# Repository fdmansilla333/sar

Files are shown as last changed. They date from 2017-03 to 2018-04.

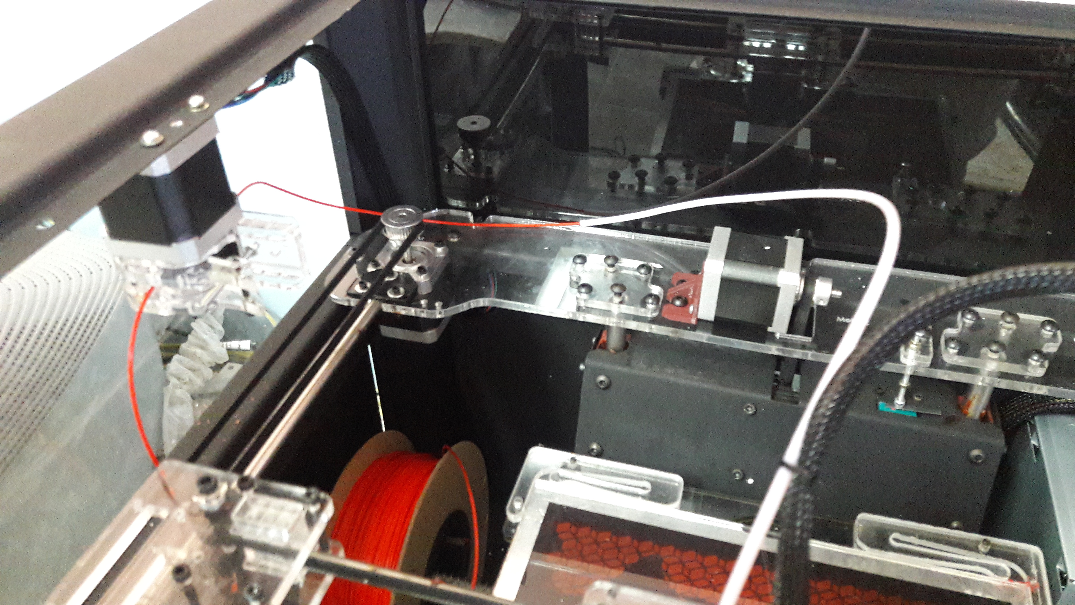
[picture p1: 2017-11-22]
Material/20170808_095417.jpg

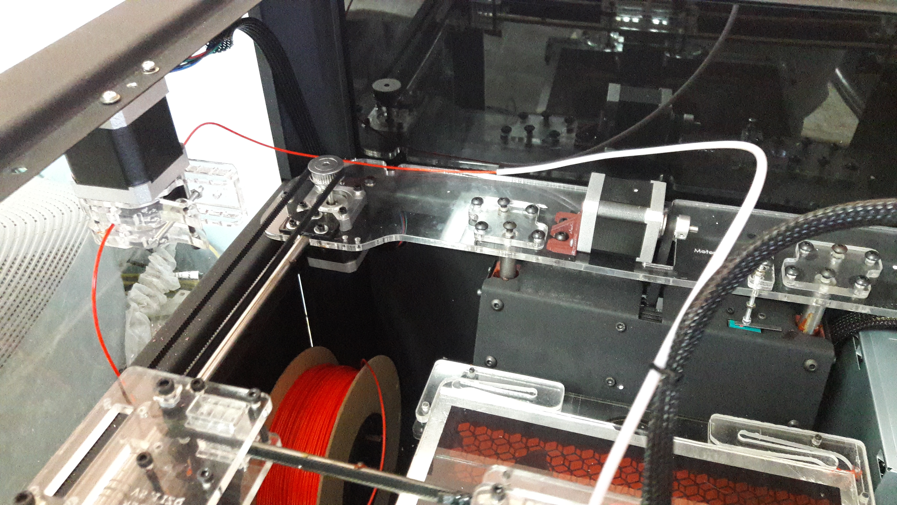
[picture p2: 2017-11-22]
Material/20170808_095419.jpg

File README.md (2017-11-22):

# sar
Sistema Autónomo Robótico

Autores:
->Mansilla Damián
->Schlapp Agustin

*Directorios
#App
Posee la aplicación y las pruebas sobre Nodejs, Johnny-five, Angular4.5, Mongo, Express. (Stack MEAN)

#Capitulos
Posee los capítulos del informe de la Tesis

#Documentacion
Contiene la documentación de los códigos fuentes de Arduino.

#Material
Contiene material bibliografíco

#Modelos3d
Posee los modelos realizados con Sketchup (diseños --> STL) y Cura (STL -> Gcode) para imprimir en 3d.

#Plantilla de casos de prueba de sensores y actuadores
Contiene todos los casos de prueba realizados sobre los sensores y actuadores. Las pruebas testean el funcionamiento básico.

#Test de sensores y actuadores Arduino
Contiene todos los códigos de prueba sobre cada actuador y sensor compatible con Arduino.

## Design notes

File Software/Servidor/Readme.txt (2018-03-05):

Comando para importar datos a mongo un arreglo json
mongoimport -c temperaturas -d sar --mode upsert --file temperaturas.json --jsonArray
Para iniciar ejecutar iniciar.bat(Windows) iniciar.sh(linux)

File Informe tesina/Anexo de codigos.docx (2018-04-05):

# Anexo de códigos

En este anexo se adjuntaron los códigos más relevantes, tanto del lado del cliente como del servidor, que se desarrollaron para el funcionamiento del SAR.

## Códigos del lado del servidor

### Código StandarFirmata utilizado en el Arduino MEGA

/*

Firmata is a generic protocol for communicating with microcontrollers

from software on a host computer. It is intended to work with

any host computer software package.

To download a host software package, please click on the following link

to open the list of Firmata client libraries in your default browser.

https://github.com/firmata/arduino#firmata-client-libraries

Copyright (C) 2006-2008 Hans-Christoph Steiner. All rights reserved.

Copyright (C) 2010-2011 Paul Stoffregen. All rights reserved.

Copyright (C) 2009 Shigeru Kobayashi. All rights reserved.

Copyright (C) 2009-2016 Jeff Hoefs. All rights reserved.

This library is free software; you can redistribute it and/or

modify it under the terms of the GNU Lesser General Public

License as published by the Free Software Foundation; either

version 2.1 of the License, or (at your option) any later version.

See file LICENSE.txt for further informations on licensing terms.

Last updated October 16th, 2016

*/

#include <Servo.h>

#include <Wire.h>

#include <Firmata.h>

#define I2C_WRITE B00000000

#define I2C_READ B00001000

#define I2C_READ_CONTINUOUSLY B00010000

#define I2C_STOP_READING B00011000

#define I2C_READ_WRITE_MODE_MASK B00011000

#define I2C_10BIT_ADDRESS_MODE_MASK B00100000

#define I2C_END_TX_MASK B01000000

#define I2C_STOP_TX 1

#define I2C_RESTART_TX 0

#define I2C_MAX_QUERIES 8

#define I2C_REGISTER_NOT_SPECIFIED -1

// the minimum interval for sampling analog input

#define MINIMUM_SAMPLING_INTERVAL 1

/*==============================================================================

* GLOBAL VARIABLES

*============================================================================*/

#ifdef FIRMATA_SERIAL_FEATURE

SerialFirmata serialFeature;

#endif

/* analog inputs */

int analogInputsToReport = 0; // bitwise array to store pin reporting

/* digital input ports */

byte reportPINs[TOTAL_PORTS]; // 1 = report this port, 0 = silence

byte previousPINs[TOTAL_PORTS]; // previous 8 bits sent

/* pins configuration */

byte portConfigInputs[TOTAL_PORTS]; // each bit: 1 = pin in INPUT, 0 = anything else

/* timer variables */

unsigned long currentMillis; // store the current value from millis()

unsigned long previousMillis; // for comparison with currentMillis

unsigned int samplingInterval = 19; // how often to run the main loop (in ms)

/* i2c data */

struct i2c_device_info {

byte addr;

int reg;

byte bytes;

byte stopTX;

};

/* for i2c read continuous more */

i2c_device_info query[I2C_MAX_QUERIES];

byte i2cRxData[64];

boolean isI2CEnabled = false;

signed char queryIndex = -1;

// default delay time between i2c read request and Wire.requestFrom()

unsigned int i2cReadDelayTime = 0;

Servo servos[MAX_SERVOS];

byte servoPinMap[TOTAL_PINS];

byte detachedServos[MAX_SERVOS];

byte detachedServoCount = 0;

byte servoCount = 0;

boolean isResetting = false;

// Forward declare a few functions to avoid compiler errors with older versions

// of the Arduino IDE.

void setPinModeCallback(byte, int);

void reportAnalogCallback(byte analogPin, int value);

void sysexCallback(byte, byte, byte*);

/* utility functions */

void wireWrite(byte data)

{

#if ARDUINO >= 100

Wire.write((byte)data);

#else

Wire.send(data);

#endif

}

byte wireRead(void)

{

#if ARDUINO >= 100

return Wire.read();

#else

return Wire.receive();

#endif

}

/*==============================================================================

* FUNCTIONS

*============================================================================*/

void attachServo(byte pin, int minPulse, int maxPulse)

{

if (servoCount < MAX_SERVOS) {

// reuse indexes of detached servos until all have been reallocated

if (detachedServoCount > 0) {

servoPinMap[pin] = detachedServos[detachedServoCount - 1];

if (detachedServoCount > 0) detachedServoCount--;

} else {

servoPinMap[pin] = servoCount;

servoCount++;

}

if (minPulse > 0 && maxPulse > 0) {

servos[servoPinMap[pin]].attach(PIN_TO_DIGITAL(pin), minPulse, maxPulse);

} else {

servos[servoPinMap[pin]].attach(PIN_TO_DIGITAL(pin));

}

} else {

Firmata.sendString("Max servos attached");

}

}

void detachServo(byte pin)

{

servos[servoPinMap[pin]].detach();

// if we're detaching the last servo, decrement the count

// otherwise store the index of the detached servo

if (servoPinMap[pin] == servoCount && servoCount > 0) {

servoCount--;

} else if (servoCount > 0) {

// keep track of detached servos because we want to reuse their indexes

// before incrementing the count of attached servos

detachedServoCount++;

detachedServos[detachedServoCount - 1] = servoPinMap[pin];

}

servoPinMap[pin] = 255;

}

void enableI2CPins()

{

byte i;

// is there a faster way to do this? would probaby require importing

// Arduino.h to get SCL and SDA pins

for (i = 0; i < TOTAL_PINS; i++) {

if (IS_PIN_I2C(i)) {

// mark pins as i2c so they are ignore in non i2c data requests

setPinModeCallback(i, PIN_MODE_I2C);

}

}

isI2CEnabled = true;

Wire.begin();

}

/* disable the i2c pins so they can be used for other functions */

void disableI2CPins() {

isI2CEnabled = false;

// disable read continuous mode for all devices

queryIndex = -1;

}

void readAndReportData(byte address, int theRegister, byte numBytes, byte stopTX) {

// allow I2C requests that don't require a register read

// for example, some devices using an interrupt pin to signify new data available

// do not always require the register read so upon interrupt you call Wire.requestFrom()

if (theRegister != I2C_REGISTER_NOT_SPECIFIED) {

Wire.beginTransmission(address);

wireWrite((byte)theRegister);

Wire.endTransmission(stopTX); // default = true

// do not set a value of 0

if (i2cReadDelayTime > 0) {

// delay is necessary for some devices such as WiiNunchuck

delayMicroseconds(i2cReadDelayTime);

}

} else {

theRegister = 0; // fill the register with a dummy value

}

Wire.requestFrom(address, numBytes); // all bytes are returned in requestFrom

// check to be sure correct number of bytes were returned by slave

if (numBytes < Wire.available()) {

Firmata.sendString("I2C: Too many bytes received");

} else if (numBytes > Wire.available()) {

Firmata.sendString("I2C: Too few bytes received");

}

i2cRxData[0] = address;

i2cRxData[1] = theRegister;

for (int i = 0; i < numBytes && Wire.available(); i++) {

i2cRxData[2 + i] = wireRead();

}

// send slave address, register and received bytes

Firmata.sendSysex(SYSEX_I2C_REPLY, numBytes + 2, i2cRxData);

}

void outputPort(byte portNumber, byte portValue, byte forceSend)

{

// pins not configured as INPUT are cleared to zeros

portValue = portValue & portConfigInputs[portNumber];

// only send if the value is different than previously sent

if (forceSend || previousPINs[portNumber] != portValue) {

Firmata.sendDigitalPort(portNumber, portValue);

previousPINs[portNumber] = portValue;

}

}

/* -----------------------------------------------------------------------------

* check all the active digital inputs for change of state, then add any events

* to the Serial output queue using Serial.print() */

void checkDigitalInputs(void)

{

/* Using non-looping code allows constants to be given to readPort().

* The compiler will apply substantial optimizations if the inputs

* to readPort() are compile-time constants. */

if (TOTAL_PORTS > 0 && reportPINs[0]) outputPort(0, readPort(0, portConfigInputs[0]), false);

if (TOTAL_PORTS > 1 && reportPINs[1]) outputPort(1, readPort(1, portConfigInputs[1]), false);

if (TOTAL_PORTS > 2 && reportPINs[2]) outputPort(2, readPort(2, portConfigInputs[2]), false);

if (TOTAL_PORTS > 3 && reportPINs[3]) outputPort(3, readPort(3, portConfigInputs[3]), false);

if (TOTAL_PORTS > 4 && reportPINs[4]) outputPort(4, readPort(4, portConfigInputs[4]), false);

if (TOTAL_PORTS > 5 && reportPINs[5]) outputPort(5, readPort(5, portConfigInputs[5]), false);

if (TOTAL_PORTS > 6 && reportPINs[6]) outputPort(6, readPort(6, portConfigInputs[6]), false);

if (TOTAL_PORTS > 7 && reportPINs[7]) outputPort(7, readPort(7, portConfigInputs[7]), false);

if (TOTAL_PORTS > 8 && reportPINs[8]) outputPort(8, readPort(8, portConfigInputs[8]), false);

if (TOTAL_PORTS > 9 && reportPINs[9]) outputPort(9, readPort(9, portConfigInputs[9]), false);

if (TOTAL_PORTS > 10 && reportPINs[10]) outputPort(10, readPort(10, portConfigInputs[10]), false);

if (TOTAL_PORTS > 11 && reportPINs[11]) outputPort(11, readPort(11, portConfigInputs[11]), false);

if (TOTAL_PORTS > 12 && reportPINs[12]) outputPort(12, readPort(12, portConfigInputs[12]), false);

if (TOTAL_PORTS > 13 && reportPINs[13]) outputPort(13, readPort(13, portConfigInputs[13]), false);

if (TOTAL_PORTS > 14 && reportPINs[14]) outputPort(14, readPort(14, portConfigInputs[14]), false);

if (TOTAL_PORTS > 15 && reportPINs[15]) outputPort(15, readPort(15, portConfigInputs[15]), false);

}

// -----------------------------------------------------------------------------

/* sets the pin mode to the correct state and sets the relevant bits in the

* two bit-arrays that track Digital I/O and PWM status

*/

void setPinModeCallback(byte pin, int mode)

{

if (Firmata.getPinMode(pin) == PIN_MODE_IGNORE)

return;

if (Firmata.getPinMode(pin) == PIN_MODE_I2C && isI2CEnabled && mode != PIN_MODE_I2C) {

// disable i2c so pins can be used for other functions

// the following if statements should reconfigure the pins properly

disableI2CPins();

}

if (IS_PIN_DIGITAL(pin) && mode != PIN_MODE_SERVO) {

if (servoPinMap[pin] < MAX_SERVOS && servos[servoPinMap[pin]].attached()) {

detachServo(pin);

}

}

if (IS_PIN_ANALOG(pin)) {

reportAnalogCallback(PIN_TO_ANALOG(pin), mode == PIN_MODE_ANALOG ? 1 : 0); // turn on/off reporting

}

if (IS_PIN_DIGITAL(pin)) {

if (mode == INPUT || mode == PIN_MODE_PULLUP) {

portConfigInputs[pin / 8] |= (1 << (pin & 7));

} else {

portConfigInputs[pin / 8] &= ~(1 << (pin & 7));

}

}

Firmata.setPinState(pin, 0);

switch (mode) {

case PIN_MODE_ANALOG:

if (IS_PIN_ANALOG(pin)) {

if (IS_PIN_DIGITAL(pin)) {

pinMode(PIN_TO_DIGITAL(pin), INPUT); // disable output driver

#if ARDUINO <= 100

// deprecated since Arduino 1.0.1 - TODO: drop support in Firmata 2.6

digitalWrite(PIN_TO_DIGITAL(pin), LOW); // disable internal pull-ups

#endif

}

Firmata.setPinMode(pin, PIN_MODE_ANALOG);

}

break;

case INPUT:

if (IS_PIN_DIGITAL(pin)) {

pinMode(PIN_TO_DIGITAL(pin), INPUT); // disable output driver

#if ARDUINO <= 100

// deprecated since Arduino 1.0.1 - TODO: drop support in Firmata 2.6

digitalWrite(PIN_TO_DIGITAL(pin), LOW); // disable internal pull-ups

#endif

Firmata.setPinMode(pin, INPUT);

}

break;

case PIN_MODE_PULLUP:

if (IS_PIN_DIGITAL(pin)) {

pinMode(PIN_TO_DIGITAL(pin), INPUT_PULLUP);

Firmata.setPinMode(pin, PIN_MODE_PULLUP);

Firmata.setPinState(pin, 1);

}

break;

case OUTPUT:

if (IS_PIN_DIGITAL(pin)) {

if (Firmata.getPinMode(pin) == PIN_MODE_PWM) {

// Disable PWM if pin mode was previously set to PWM.

digitalWrite(PIN_TO_DIGITAL(pin), LOW);

}

pinMode(PIN_TO_DIGITAL(pin), OUTPUT);

Firmata.setPinMode(pin, OUTPUT);

}

break;

case PIN_MODE_PWM:

if (IS_PIN_PWM(pin)) {

pinMode(PIN_TO_PWM(pin), OUTPUT);

analogWrite(PIN_TO_PWM(pin), 0);

Firmata.setPinMode(pin, PIN_MODE_PWM);

}

break;

case PIN_MODE_SERVO:

if (IS_PIN_DIGITAL(pin)) {

Firmata.setPinMode(pin, PIN_MODE_SERVO);

if (servoPinMap[pin] == 255 || !servos[servoPinMap[pin]].attached()) {

// pass -1 for min and max pulse values to use default values set

// by Servo library

attachServo(pin, -1, -1);

}

}

break;

case PIN_MODE_I2C:

if (IS_PIN_I2C(pin)) {

// mark the pin as i2c

// the user must call I2C_CONFIG to enable I2C for a device

Firmata.setPinMode(pin, PIN_MODE_I2C);

}

break;

case PIN_MODE_SERIAL:

#ifdef FIRMATA_SERIAL_FEATURE

serialFeature.handlePinMode(pin, PIN_MODE_SERIAL);

#endif

break;

default:

Firmata.sendString("Unknown pin mode"); // TODO: put error msgs in EEPROM

}

// TODO: save status to EEPROM here, if changed

}

/*

* Sets the value of an individual pin. Useful if you want to set a pin value but

* are not tracking the digital port state.

* Can only be used on pins configured as OUTPUT.

* Cannot be used to enable pull-ups on Digital INPUT pins.

*/

void setPinValueCallback(byte pin, int value)

{

if (pin < TOTAL_PINS && IS_PIN_DIGITAL(pin)) {

if (Firmata.getPinMode(pin) == OUTPUT) {

Firmata.setPinState(pin, value);

digitalWrite(PIN_TO_DIGITAL(pin), value);

}

}

}

void analogWriteCallback(byte pin, int value)

{

if (pin < TOTAL_PINS) {

switch (Firmata.getPinMode(pin)) {

case PIN_MODE_SERVO:

if (IS_PIN_DIGITAL(pin))

servos[servoPinMap[pin]].write(value);

Firmata.setPinState(pin, value);

break;

case PIN_MODE_PWM:

if (IS_PIN_PWM(pin))

analogWrite(PIN_TO_PWM(pin), value);

Firmata.setPinState(pin, value);

break;

}

}

}

void digitalWriteCallback(byte port, int value)

{

byte pin, lastPin, pinValue, mask = 1, pinWriteMask = 0;

if (port < TOTAL_PORTS) {

// create a mask of the pins on this port that are writable.

lastPin = port * 8 + 8;

if (lastPin > TOTAL_PINS) lastPin = TOTAL_PINS;

for (pin = port * 8; pin < lastPin; pin++) {

// do not disturb non-digital pins (eg, Rx & Tx)

if (IS_PIN_DIGITAL(pin)) {

// do not touch pins in PWM, ANALOG, SERVO or other modes

if (Firmata.getPinMode(pin) == OUTPUT || Firmata.getPinMode(pin) == INPUT) {

pinValue = ((byte)value & mask) ? 1 : 0;

if (Firmata.getPinMode(pin) == OUTPUT) {

pinWriteMask |= mask;

} else if (Firmata.getPinMode(pin) == INPUT && pinValue == 1 && Firmata.getPinState(pin) != 1) {

// only handle INPUT here for backwards compatibility

#if ARDUINO > 100

pinMode(pin, INPUT_PULLUP);

#else

// only write to the INPUT pin to enable pullups if Arduino v1.0.0 or earlier

pinWriteMask |= mask;

#endif

}

Firmata.setPinState(pin, pinValue);

}

}

mask = mask << 1;

}

writePort(port, (byte)value, pinWriteMask);

}

}

// -----------------------------------------------------------------------------

/* sets bits in a bit array (int) to toggle the reporting of the analogIns

*/

//void FirmataClass::setAnalogPinReporting(byte pin, byte state) {

//}

void reportAnalogCallback(byte analogPin, int value)

{

if (analogPin < TOTAL_ANALOG_PINS) {

if (value == 0) {

analogInputsToReport = analogInputsToReport & ~ (1 << analogPin);

} else {

analogInputsToReport = analogInputsToReport | (1 << analogPin);

// prevent during system reset or all analog pin values will be reported

// which may report noise for unconnected analog pins

if (!isResetting) {

// Send pin value immediately. This is helpful when connected via

// ethernet, wi-fi or bluetooth so pin states can be known upon

// reconnecting.

Firmata.sendAnalog(analogPin, analogRead(analogPin));

}

}

}

// TODO: save status to EEPROM here, if changed

}

void reportDigitalCallback(byte port, int value)

{

if (port < TOTAL_PORTS) {

reportPINs[port] = (byte)value;

// Send port value immediately. This is helpful when connected via

// ethernet, wi-fi or bluetooth so pin states can be known upon

// reconnecting.

if (value) outputPort(port, readPort(port, portConfigInputs[port]), true);

}

// do not disable analog reporting on these 8 pins, to allow some

// pins used for digital, others analog. Instead, allow both types

// of reporting to be enabled, but check if the pin is configured

// as analog when sampling the analog inputs. Likewise, while

// scanning digital pins, portConfigInputs will mask off values from any

// pins configured as analog

}

/*==============================================================================

* SYSEX-BASED commands

*============================================================================*/

void sysexCallback(byte command, byte argc, byte *argv)

{

byte mode;

byte stopTX;

byte slaveAddress;

byte data;

int slaveRegister;

unsigned int delayTime;

switch (command) {

case I2C_REQUEST:

mode = argv[1] & I2C_READ_WRITE_MODE_MASK;

if (argv[1] & I2C_10BIT_ADDRESS_MODE_MASK) {

Firmata.sendString("10-bit addressing not supported");

return;

}

else {

slaveAddress = argv[0];

}

// need to invert the logic here since 0 will be default for client

// libraries that have not updated to add support for restart tx

if (argv[1] & I2C_END_TX_MASK) {

stopTX = I2C_RESTART_TX;

}

else {

stopTX = I2C_STOP_TX; // default

}

switch (mode) {

case I2C_WRITE:

Wire.beginTransmission(slaveAddress);

for (byte i = 2; i < argc; i += 2) {

data = argv[i] + (argv[i + 1] << 7);

wireWrite(data);

}

Wire.endTransmission();

delayMicroseconds(70);

break;

case I2C_READ:

if (argc == 6) {

// a slave register is specified

slaveRegister = argv[2] + (argv[3] << 7);

data = argv[4] + (argv[5] << 7); // bytes to read

}

else {

// a slave register is NOT specified

slaveRegister = I2C_REGISTER_NOT_SPECIFIED;

data = argv[2] + (argv[3] << 7); // bytes to read

}

readAndReportData(slaveAddress, (int)slaveRegister, data, stopTX);

break;

case I2C_READ_CONTINUOUSLY:

if ((queryIndex + 1) >= I2C_MAX_QUERIES) {

// too many queries, just ignore

Firmata.sendString("too many queries");

break;

}

if (argc == 6) {

// a slave register is specified

slaveRegister = argv[2] + (argv[3] << 7);

data = argv[4] + (argv[5] << 7); // bytes to read

}

else {

// a slave register is NOT specified

slaveRegister = (int)I2C_REGISTER_NOT_SPECIFIED;

data = argv[2] + (argv[3] << 7); // bytes to read

}

queryIndex++;

query[queryIndex].addr = slaveAddress;

query[queryIndex].reg = slaveRegister;

query[queryIndex].bytes = data;

query[queryIndex].stopTX = stopTX;

break;

case I2C_STOP_READING:

byte queryIndexToSkip;

// if read continuous mode is enabled for only 1 i2c device, disable

// read continuous reporting for that device

if (queryIndex <= 0) {

queryIndex = -1;

} else {

queryIndexToSkip = 0;

// if read continuous mode is enabled for multiple devices,

// determine which device to stop reading and remove it's data from

// the array, shifiting other array data to fill the space

for (byte i = 0; i < queryIndex + 1; i++) {

if (query[i].addr == slaveAddress) {

queryIndexToSkip = i;

break;

}

}

for (byte i = queryIndexToSkip; i < queryIndex + 1; i++) {

if (i < I2C_MAX_QUERIES) {

query[i].addr = query[i + 1].addr;

query[i].reg = query[i + 1].reg;

query[i].bytes = query[i + 1].bytes;

query[i].stopTX = query[i + 1].stopTX;

}

}

queryIndex--;

}

break;

default:

break;

}

break;

case I2C_CONFIG:

delayTime = (argv[0] + (argv[1] << 7));

if (delayTime > 0) {

i2cReadDelayTime = delayTime;

}

if (!isI2CEnabled) {

enableI2CPins();

}

break;

case SERVO_CONFIG:

if (argc > 4) {

// these vars are here for clarity, they'll optimized away by the compiler

byte pin = argv[0];

int minPulse = argv[1] + (argv[2] << 7);

int maxPulse = argv[3] + (argv[4] << 7);

if (IS_PIN_DIGITAL(pin)) {

if (servoPinMap[pin] < MAX_SERVOS && servos[servoPinMap[pin]].attached()) {

detachServo(pin);

}

attachServo(pin, minPulse, maxPulse);

setPinModeCallback(pin, PIN_MODE_SERVO);

}

}

break;

case SAMPLING_INTERVAL:

if (argc > 1) {

samplingInterval = argv[0] + (argv[1] << 7);

if (samplingInterval < MINIMUM_SAMPLING_INTERVAL) {

samplingInterval = MINIMUM_SAMPLING_INTERVAL;

}

} else {

//Firmata.sendString("Not enough data");

}

break;

case EXTENDED_ANALOG:

if (argc > 1) {

int val = argv[1];

if (argc > 2) val |= (argv[2] << 7);

if (argc > 3) val |= (argv[3] << 14);

analogWriteCallback(argv[0], val);

}

break;

case CAPABILITY_QUERY:

Firmata.write(START_SYSEX);

Firmata.write(CAPABILITY_RESPONSE);

for (byte pin = 0; pin < TOTAL_PINS; pin++) {

if (IS_PIN_DIGITAL(pin)) {

Firmata.write((byte)INPUT);

Firmata.write(1);

Firmata.write((byte)PIN_MODE_PULLUP);

Firmata.write(1);

Firmata.write((byte)OUTPUT);

Firmata.write(1);

}

if (IS_PIN_ANALOG(pin)) {

Firmata.write(PIN_MODE_ANALOG);

Firmata.write(10); // 10 = 10-bit resolution

}

if (IS_PIN_PWM(pin)) {

Firmata.write(PIN_MODE_PWM);

Firmata.write(DEFAULT_PWM_RESOLUTION);

}

if (IS_PIN_DIGITAL(pin)) {

Firmata.write(PIN_MODE_SERVO);

Firmata.write(14);

}

if (IS_PIN_I2C(pin)) {

Firmata.write(PIN_MODE_I2C);

Firmata.write(1); // TODO: could assign a number to map to SCL or SDA

}

#ifdef FIRMATA_SERIAL_FEATURE

serialFeature.handleCapability(pin);

#endif

Firmata.write(127);

}

Firmata.write(END_SYSEX);

break;

case PIN_STATE_QUERY:

if (argc > 0) {

byte pin = argv[0];

Firmata.write(START_SYSEX);

Firmata.write(PIN_STATE_RESPONSE);

Firmata.write(pin);

if (pin < TOTAL_PINS) {

Firmata.write(Firmata.getPinMode(pin));

Firmata.write((byte)Firmata.getPinState(pin) & 0x7F);

if (Firmata.getPinState(pin) & 0xFF80) Firmata.write((byte)(Firmata.getPinState(pin) >> 7) & 0x7F);

if (Firmata.getPinState(pin) & 0xC000) Firmata.write((byte)(Firmata.getPinState(pin) >> 14) & 0x7F);

}

Firmata.write(END_SYSEX);

}

break;

case ANALOG_MAPPING_QUERY:

Firmata.write(START_SYSEX);

Firmata.write(ANALOG_MAPPING_RESPONSE);

for (byte pin = 0; pin < TOTAL_PINS; pin++) {

Firmata.write(IS_PIN_ANALOG(pin) ? PIN_TO_ANALOG(pin) : 127);

}

Firmata.write(END_SYSEX);

break;

case SERIAL_MESSAGE:

#ifdef FIRMATA_SERIAL_FEATURE

serialFeature.handleSysex(command, argc, argv);

#endif

break;

}

}

/*==============================================================================

* SETUP()

*============================================================================*/

void systemResetCallback()

{

isResetting = true;

// initialize a defalt state

// TODO: option to load config from EEPROM instead of default

#ifdef FIRMATA_SERIAL_FEATURE

serialFeature.reset();

#endif

if (isI2CEnabled) {

disableI2CPins();

}

for (byte i = 0; i < TOTAL_PORTS; i++) {

reportPINs[i] = false; // by default, reporting off

portConfigInputs[i] = 0; // until activated

previousPINs[i] = 0;

}

for (byte i = 0; i < TOTAL_PINS; i++) {

// pins with analog capability default to analog input

// otherwise, pins default to digital output

if (IS_PIN_ANALOG(i)) {

// turns off pullup, configures everything

setPinModeCallback(i, PIN_MODE_ANALOG);

} else if (IS_PIN_DIGITAL(i)) {

// sets the output to 0, configures portConfigInputs

setPinModeCallback(i, OUTPUT);

}

servoPinMap[i] = 255;

}

// by default, do not report any analog inputs

analogInputsToReport = 0;

detachedServoCount = 0;

servoCount = 0;

/* send digital inputs to set the initial state on the host computer,

* since once in the loop(), this firmware will only send on change */

/*

TODO: this can never execute, since no pins default to digital input

but it will be needed when/if we support EEPROM stored config

for (byte i=0; i < TOTAL_PORTS; i++) {

outputPort(i, readPort(i, portConfigInputs[i]), true);

}

*/

isResetting = false;

}

void setup()

{

Firmata.setFirmwareVersion(FIRMATA_FIRMWARE_MAJOR_VERSION, FIRMATA_FIRMWARE_MINOR_VERSION);

Firmata.attach(ANALOG_MESSAGE, analogWriteCallback);

Firmata.attach(DIGITAL_MESSAGE, digitalWriteCallback);

Firmata.attach(REPORT_ANALOG, reportAnalogCallback);

Firmata.attach(REPORT_DIGITAL, reportDigitalCallback);

Firmata.attach(SET_PIN_MODE, setPinModeCallback);

Firmata.attach(SET_DIGITAL_PIN_VALUE, setPinValueCallback);

Firmata.attach(START_SYSEX, sysexCallback);

Firmata.attach(SYSTEM_RESET, systemResetCallback);

// to use a port other than Serial, such as Serial1 on an Arduino Leonardo or Mega,

// Call begin(baud) on the alternate serial port and pass it to Firmata to begin like this:

// Serial1.begin(57600);

// Firmata.begin(Serial1);

// However do not do this if you are using SERIAL_MESSAGE

Firmata.begin(57600);

while (!Serial) {

; // wait for serial port to connect. Needed for ATmega32u4-based boards and Arduino 101

}

systemResetCallback(); // reset to default config

}

/*==============================================================================

* LOOP()

*============================================================================*/

void loop()

{

byte pin, analogPin;

/* DIGITALREAD - as fast as possible, check for changes and output them to the

* FTDI buffer using Serial.print() */

checkDigitalInputs();

/* STREAMREAD - processing incoming messagse as soon as possible, while still

* checking digital inputs. */

while (Firmata.available())

Firmata.processInput();

// TODO - ensure that Stream buffer doesn't go over 60 bytes

currentMillis = millis();

if (currentMillis - previousMillis > samplingInterval) {

previousMillis += samplingInterval;

/* ANALOGREAD - do all analogReads() at the configured sampling interval */

for (pin = 0; pin < TOTAL_PINS; pin++) {

if (IS_PIN_ANALOG(pin) && Firmata.getPinMode(pin) == PIN_MODE_ANALOG) {

analogPin = PIN_TO_ANALOG(pin);

if (analogInputsToReport & (1 << analogPin)) {

Firmata.sendAnalog(analogPin, analogRead(analogPin));

}

}

}

// report i2c data for all device with read continuous mode enabled

if (queryIndex > -1) {

for (byte i = 0; i < queryIndex + 1; i++) {

readAndReportData(query[i].addr, query[i].reg, query[i].bytes, query[i].stopTX);

}

}

}

#ifdef FIRMATA_SERIAL_FEATURE

serialFeature.update();

#endif

}

### Código ConfigurableFirmata utilizado en el Arduino NANO

/*

Firmata is a generic protocol for communicating with microcontrollers

from software on a host computer. It is intended to work with

any host computer software package.

To download a host software package, please clink on the following link

to open the download page in your default browser.

https://github.com/firmata/ConfigurableFirmata#firmata-client-libraries

Copyright (C) 2006-2008 Hans-Christoph Steiner. All rights reserved.

Copyright (C) 2010-2011 Paul Stoffregen. All rights reserved.

Copyright (C) 2009 Shigeru Kobayashi. All rights reserved.

Copyright (C) 2013 Norbert Truchsess. All rights reserved.

Copyright (C) 2014 Nicolas Panel. All rights reserved.

Copyright (C) 2009-2017 Jeff Hoefs. All rights reserved.

This library is free software; you can redistribute it and/or

modify it under the terms of the GNU Lesser General Public

License as published by the Free Software Foundation; either

version 2.1 of the License, or (at your option) any later version.

See file LICENSE.txt for further informations on licensing terms.

Last updated: September 16th, 2017

*/

/*

README

This is an example use of ConfigurableFirmata. The easiest way to create a configuration is to

use http://firmatabuilder.com and select the communication transport and the firmata features

to include and an Arduino sketch (.ino) file will be generated and downloaded automatically.

To manually configure a sketch, copy this file and follow the instructions in the

ETHERNET CONFIGURATION OPTION (if you want to use Ethernet instead of Serial/USB) and

FIRMATA FEATURE CONFIGURATION sections in this file.

*/

#include "ConfigurableFirmata.h"

/*==============================================================================

* ETHERNET CONFIGURATION OPTION

*

* By default Firmata uses the Serial-port (over USB) of the Arduino. ConfigurableFirmata may also

* comunicate over ethernet using tcp/ip. To configure this sketch to use Ethernet instead of

* Serial, uncomment the approprate includes for your particular hardware. See STEPS 1 - 5 below.

* If you want to use Serial (over USB) then skip ahead to the FIRMATA FEATURE CONFIGURATION

* section further down in this file.

*

* If you enable Ethernet, you will need a Firmata client library with a network transport that can

* act as a server in order to establish a connection between ConfigurableFirmataEthernet and the

* Firmata host application (your application).

*

* To use ConfigurableFirmata with Ethernet you will need to have one of the following

* boards or shields:

*

* - Arduino Ethernet shield (or clone)

* - Arduino Ethernet board (or clone)

* - Arduino Yun

*

* If you are using an Arduino Ethernet shield you cannot use the following pins on

* the following boards. Firmata will ignore any requests to use these pins:

*

* - Arduino Uno or other ATMega328 boards: (D4, D10, D11, D12, D13)

* - Arduino Mega: (D4, D10, D50, D51, D52, D53)

* - Arduino Leonardo: (D4, D10)

* - Arduino Due: (D4, D10)

* - Arduino Zero: (D4, D10)

*

* If you are using an ArduinoEthernet board, the following pins cannot be used (same as Uno):

* - D4, D10, D11, D12, D13

*============================================================================*/

// STEP 1 [REQUIRED]

// Uncomment / comment the appropriate set of includes for your hardware (OPTION A, B or C)

/*

* OPTION A: Configure for Arduino Ethernet board or Arduino Ethernet shield (or clone)

*

* To configure ConfigurableFirmata to use the an Arduino Ethernet Shield or Arduino Ethernet

* Board (both use the same WIZ5100-based Ethernet controller), uncomment the SPI and Ethernet

* includes below.

*/

//#include <SPI.h>

//#include <Ethernet.h>

/*

* OPTION B: Configure for a board or shield using an ENC28J60-based Ethernet controller,

* uncomment out the UIPEthernet include below.

*

* The UIPEthernet-library can be downloaded

* from: https://github.com/ntruchsess/arduino_uip

*/

//#include <UIPEthernet.h>

/*

* OPTION C: Configure for Arduino Yun

*

* The Ethernet port on the Arduino Yun board can be used with Firmata in this configuration.

* To execute StandardFirmataEthernet on Yun uncomment the Bridge and YunClient includes below.

*

* NOTE: in order to compile for the Yun you will also need to comment out some of the includes

* and declarations in the FIRMATA FEATURE CONFIGURATION section later in this file. Including all

* features exceeds the RAM and Flash memory of the Yun. Comment out anything you don't need.

*

* On Yun there's no need to configure local_ip and mac address as this is automatically

* configured on the linux-side of Yun.

*

* Establishing a connection with the Yun may take several seconds.

*/

//#include <Bridge.h>

//#include <YunClient.h>

#if defined ethernet_h || defined UIPETHERNET_H || defined _YUN_CLIENT_H_

#define NETWORK_FIRMATA

// STEP 2 [REQUIRED for all boards and shields]

// replace with IP of the server you want to connect to, comment out if using 'remote_host'

#define remote_ip IPAddress(192, 168, 0, 1)

// OR replace with hostname of server you want to connect to, comment out if using 'remote_ip'

// #define remote_host "server.local"

// STEP 3 [REQUIRED unless using Arduino Yun]

// Replace with the port that your server is listening on

#define remote_port 3030

// STEP 4 [REQUIRED unless using Arduino Yun OR if not using DHCP]

// Replace with your board or Ethernet shield's IP address

// Comment out if you want to use DHCP

#define local_ip IPAddress(192, 168, 0, 6)

// STEP 5 [REQUIRED unless using Arduino Yun]

// replace with Ethernet shield mac. Must be unique for your network

const byte mac[] = {0x90, 0xA2, 0xDA, 0x0D, 0x07, 0x02};

#endif

/*==============================================================================

* FIRMATA FEATURE CONFIGURATION

*

* Comment out the include and declaration for any features that you do not need

* below.

*

* WARNING: Including all of the following features (especially if also using

* Ethernet) may exceed the Flash and/or RAM of lower memory boards such as the

* Arduino Uno or Leonardo.

*============================================================================*/

#include <DigitalInputFirmata.h>

DigitalInputFirmata digitalInput;

#include <DigitalOutputFirmata.h>

DigitalOutputFirmata digitalOutput;

#include <AnalogInputFirmata.h>

AnalogInputFirmata analogInput;

#include <AnalogOutputFirmata.h>

AnalogOutputFirmata analogOutput;

#include <Servo.h>

#include <ServoFirmata.h>

ServoFirmata servo;

// ServoFirmata depends on AnalogOutputFirmata

#if defined ServoFirmata_h && ! defined AnalogOutputFirmata_h

#error AnalogOutputFirmata must be included to use ServoFirmata

#endif

#include <Wire.h>

#include <I2CFirmata.h>

I2CFirmata i2c;

#include <OneWireFirmata.h>

OneWireFirmata oneWire;

// StepperFirmata is deprecated as of ConfigurableFirmata v2.10.0. Please update your

// client implementation to use the new, more full featured and scalable AccelStepperFirmata.

#include <StepperFirmata.h>

StepperFirmata stepper;

#include <AccelStepperFirmata.h>

AccelStepperFirmata accelStepper;

#include <SerialFirmata.h>

SerialFirmata serial;

#include <FirmataExt.h>

FirmataExt firmataExt;

#include <FirmataScheduler.h>

FirmataScheduler scheduler;

// To add Encoder support you must first install the FirmataEncoder and Encoder libraries:

// https://github.com/firmata/FirmataEncoder

// https://www.pjrc.com/teensy/td_libs_Encoder.html

// #include <Encoder.h>

// #include <FirmataEncoder.h>

// FirmataEncoder encoder;

/*===================================================================================

* END FEATURE CONFIGURATION - you should not need to change anything below this line

*==================================================================================*/

// dependencies. Do not comment out the following lines

#if defined AnalogOutputFirmata_h || defined ServoFirmata_h

#include <AnalogWrite.h>

#endif

#if defined AnalogInputFirmata_h || defined I2CFirmata_h || defined FirmataEncoder_h

#include <FirmataReporting.h>

FirmataReporting reporting;

#endif

// dependencies for Network Firmata. Do not comment out.

#ifdef NETWORK_FIRMATA

#if defined remote_ip && defined remote_host

#error "cannot define both remote_ip and remote_host at the same time!"

#endif

#include <EthernetClientStream.h>

#ifdef _YUN_CLIENT_H_

YunClient client;

#else

EthernetClient client;

#endif

#if defined remote_ip && !defined remote_host

#ifdef local_ip

EthernetClientStream stream(client, local_ip, remote_ip, NULL, remote_port);

#else

EthernetClientStream stream(client, IPAddress(0, 0, 0, 0), remote_ip, NULL, remote_port);

#endif

#endif

#if !defined remote_ip && defined remote_host

#ifdef local_ip

EthernetClientStream stream(client, local_ip, IPAddress(0, 0, 0, 0), remote_host, remote_port);

#else

EthernetClientStream stream(client, IPAddress(0, 0, 0, 0), IPAddress(0, 0, 0, 0), remote_host, remote_port);

#endif

#endif

#endif

/*==============================================================================

* FUNCTIONS

*============================================================================*/

void systemResetCallback()

{

// initialize a default state

// pins with analog capability default to analog input

// otherwise, pins default to digital output

for (byte i = 0; i < TOTAL_PINS; i++) {

if (IS_PIN_ANALOG(i)) {

#ifdef AnalogInputFirmata_h

// turns off pull-up, configures everything

Firmata.setPinMode(i, PIN_MODE_ANALOG);

#endif

} else if (IS_PIN_DIGITAL(i)) {

#ifdef DigitalOutputFirmata_h

// sets the output to 0, configures portConfigInputs

Firmata.setPinMode(i, OUTPUT);

#endif

}

}

#ifdef FirmataExt_h

firmataExt.reset();

#endif

}

/*==============================================================================

* SETUP()

*============================================================================*/

void setup()

{

/*

* ETHERNET SETUP

*/

#ifdef NETWORK_FIRMATA

#ifdef _YUN_CLIENT_H_

Bridge.begin();

#else

#ifdef local_ip

Ethernet.begin((uint8_t *)mac, local_ip); //start Ethernet

#else

Ethernet.begin((uint8_t *)mac); //start Ethernet using dhcp

#endif

#endif

delay(1000);

#endif

/*

* FIRMATA SETUP

*/

Firmata.setFirmwareVersion(FIRMATA_FIRMWARE_MAJOR_VERSION, FIRMATA_FIRMWARE_MINOR_VERSION);

#ifdef FirmataExt_h

#ifdef DigitalInputFirmata_h

firmataExt.addFeature(digitalInput);

#endif

#ifdef DigitalOutputFirmata_h

firmataExt.addFeature(digitalOutput);

#endif

#ifdef AnalogInputFirmata_h

firmataExt.addFeature(analogInput);

#endif

#ifdef AnalogOutputFirmata_h

firmataExt.addFeature(analogOutput);

#endif

#ifdef ServoFirmata_h

firmataExt.addFeature(servo);

#endif

#ifdef I2CFirmata_h

firmataExt.addFeature(i2c);

#endif

#ifdef OneWireFirmata_h

firmataExt.addFeature(oneWire);

#endif

#ifdef StepperFirmata_h

firmataExt.addFeature(stepper);

#endif

#ifdef AccelStepperFirmata_h

firmataExt.addFeature(accelStepper);

#endif

#ifdef SerialFirmata_h

firmataExt.addFeature(serial);

#endif

#ifdef FirmataReporting_h

firmataExt.addFeature(reporting);

#endif

#ifdef FirmataScheduler_h

firmataExt.addFeature(scheduler);

#endif

#ifdef FirmataEncoder_h

firmataExt.addFeature(encoder);

#endif

#endif

/* systemResetCallback is declared here (in ConfigurableFirmata.ino) */

Firmata.attach(SYSTEM_RESET, systemResetCallback);

// Network Firmata communicates with Ethernet-shields over SPI. Therefor all

// SPI-pins must be set to PIN_MODE_IGNORE. Otherwise Firmata would break SPI-communication.

// add Pin 10 and configure pin 53 as output if using a MEGA with Ethernetshield.

// No need to ignore pin 10 on MEGA with ENC28J60, as here pin 53 should be connected to SS:

#ifdef NETWORK_FIRMATA

#ifndef _YUN_CLIENT_H_

// ignore SPI and pin 4 that is SS for SD-Card on Ethernet-shield

for (byte i = 0; i < TOTAL_PINS; i++) {

if (IS_PIN_SPI(i)

|| 4 == i // SD Card on Ethernet shield uses pin 4 for SS

|| 10 == i // Ethernet-shield uses pin 10 for SS

) {

Firmata.setPinMode(i, PIN_MODE_IGNORE);

}

}

// pinMode(PIN_TO_DIGITAL(53), OUTPUT); configure hardware-SS as output on MEGA

pinMode(PIN_TO_DIGITAL(4), OUTPUT); // switch off SD-card bypassing Firmata

digitalWrite(PIN_TO_DIGITAL(4), HIGH); // SS is active low;

#endif

#if defined(__AVR_ATmega1280__) || defined(__AVR_ATmega2560__)

pinMode(PIN_TO_DIGITAL(53), OUTPUT); // configure hardware SS as output on MEGA

#endif

// start up Network Firmata:

Firmata.begin(stream);

#else

// Uncomment to save a couple of seconds by disabling the startup blink sequence.

// Firmata.disableBlinkVersion();

// start up the default Firmata using Serial interface:

Firmata.begin(57600);

#endif

systemResetCallback(); // reset to default config

}

/*==============================================================================

* LOOP()

*============================================================================*/

void loop()

{

#ifdef DigitalInputFirmata_h

/* DIGITALREAD - as fast as possible, check for changes and output them to the

* stream buffer using Firmata.write() */

digitalInput.report();

#endif

/* STREAMREAD - processing incoming message as soon as possible, while still

* checking digital inputs. */

while (Firmata.available()) {

Firmata.processInput();

#ifdef FirmataScheduler_h

if (!Firmata.isParsingMessage()) {

goto runtasks;

}

}

if (!Firmata.isParsingMessage()) {

runtasks: scheduler.runTasks();

#endif

}

/* SEND STREAM WRITE BUFFER - TO DO: make sure that the stream buffer doesn't go over

* 60 bytes. use a timer to sending an event character every 4 ms to

* trigger the buffer to dump. */

#ifdef FirmataReporting_h

if (reporting.elapsed()) {

#ifdef AnalogInputFirmata_h

/* ANALOGREAD - do all analogReads() at the configured sampling interval */

analogInput.report();

#endif

#ifdef I2CFirmata_h

// report i2c data for all device with read continuous mode enabled

i2c.report();

#endif

#ifdef FirmataEncoder_h

// report encoders positions if reporting enabled.

encoder.report();

#endif

}

#endif

#ifdef StepperFirmata_h

stepper.update();

#endif

#ifdef AccelStepperFirmata_h

accelStepper.update();

#endif

#ifdef SerialFirmata_h

serial.update();

#endif

#if defined NETWORK_FIRMATA && !defined local_ip &&!defined _YUN_CLIENT_H_

// only necessary when using DHCP, ensures local IP is updated appropriately if it changes

if (Ethernet.maintain()) {

stream.maintain(Ethernet.localIP());

}

#endif

}

### Código Servidor Node (server.js)

const express = require('express');

const bodyParser = require('body-parser');

const path = require('path');

const http = require('http');

const app = express();

// API file for interacting with MongoDB

const api = require('./server/routes/api');

// Parsers

app.use(bodyParser.json());

app.use(bodyParser.urlencoded({ extended: false}));

// Angular DIST output folder

app.use(express.static(path.join(__dirname, 'dist')));

// CORS

app.use(function(req, res, next) {

res.header("Access-Control-Allow-Origin", "*");

res.header("Access-Control-Allow-Headers", "Origin, X-Requested-With, Content-Type, Accept");

next();

});

// API location

app.use('/api', api.rutas);

app.use('/api', api.placas);

// Enviar todo lo otro a Angular

app.get('*', (req, res) => {

if (process.env.AMBIENTE == 'DESARROLLO'){

//Estoy levantando angular en puerto 4200

res.status(404).send('Estas en desarrollo');

}else{

res.sendFile(path.join(__dirname, 'dist/index.html'));

}

});

//Set Port

const port = process.env.PORT || '3000';

app.set('port', port);

const server = http.createServer(app);

server.listen(port, () => console.log(`Running on localhost:${port}`));

# Código API Express (api.js)

const express = require('express');

const router = express.Router();

const MongoClient = require('mongodb').MongoClient;

const ObjectID = require('mongodb').ObjectID;

const MINIMODISTANCIA = 20;

/*Esto es para apagar*/

const control = require('./apagar');

console.log(control.saludar());

if (process.env.AMBIENTE == 'DESARROLLO') {

console.log('Iniciado desarrollo');

var hola = require('./hola');

module.exports = hola;

} else {

console.log('Iniciado Test');

var placas = require('./placas');

module.exports.placas = placas;

}

var cont = 0;

// Connect

const connection = (closure) => {

return MongoClient.connect('mongodb://localhost:27017/sar', (err, db) => {

if (err) return console.log(err);

closure(db);

});

};

// Error handling

const sendError = (err, res) => {

response.status = 501;

response.message = typeof err == 'object' ? err.message : err;

res.status(501).json(response);

};

// Response handling

let response = {

status: 200,

data: [],

message: null

};

router.get('/temperaturas', (req, res) => {

var lista = [];

connection((db) => {

db.collection('temperaturas')

.distinct("fecha").then((fechas) => {

fechas.forEach(f => {

db.collection("temperaturas")

.find({ "fecha": f }, { "valor": 1, "hora": 1, "_id": 0 }).sort({ "fecha": 1, "hora": 1 }).batchSize(30000)

.toArray(function (err, result) {

if (err) throw err;

lista.push({ series: result, fecha: f });

if (lista.length === fechas.length) {

console.log('Mostrando ----****');

console.log(lista[5].series.length);

console.log(lista[5].fecha);

res.json(lista);

db.close();

}

});

});

})

.catch((err) => {

sendError(err, res);

})

});

});

router.get('/monoxidos', (req, res) => {

connection((db) => {

db.collection('mq7')

.find()

.toArray()

.then((valores) => {

response = valores;

res.json(response);

db.close();

})

.catch((err) => {

sendError(err, res);

});

});

});

router.get('/monoxidosActual', (req, res) => {

var ahora = new Date();

var despues = new Date();

despues.setSeconds(ahora.getSeconds() + 5);

hora1 = ahora.getHours() + ':' + ahora.getMinutes() + ':' + ahora.getSeconds();

hora2 = despues.getHours() + ':' + despues.getMinutes() + ':' + despues.getSeconds();

// console.log('Buscando con '+hora1+' y '+hora2);

connection((db) => {

db.collection('monoxidos')

.findOne({ "hora": { $gte: hora1, $lte: hora2 } }, { "valor": 1, "hora": 1, "_id": 0 },

function (err, result) {

if (err) throw err;

// console.log(result);

res.json(result);

db.close();

});

});

});

/*

Se exportan las variables para que sean conocidas por Nodejs

*/

router.get('/apagar', (req, res) => {

console.log('LLego solicitud de apagado...');

control.apagar();

});

router.get('/reiniciar', (req, res) => {

console.log('Llego solicitud de reinicio...');

control.reiniciar();

});

module.exports.rutas = router;

### Código Manejo de Arduino Mega y Arduino Nano (placas.js)

const express = require('express');

const router = express.Router();

const MongoClient = require('mongodb').MongoClient;

const ObjectID = require('mongodb').ObjectID;

const MINIMODISTANCIA = 20;

const connection = (closure) => {

return MongoClient.connect('mongodb://localhost:27017/sar', (err, db) => {

if (err) return console.log(err);

closure(db);

});

};

var ports = [{ id: "mega", port: "/dev/ttyACM0" },

{ id: "nano", port: "/dev/ttyUSB0" }

];

var five = require("johnny-five");

new five.Boards(ports).on("ready", function () {

//Se enciende la placa

var motor1;

var motor2;

var motor3;

var motor4;

// configuro el sensor de monoxido

//Se enciende la placa

var sensor = new five.Sensor({

pin: "A0",

board: this.byId("mega"),

freq: 1000 //Frecuencia en msg

});

//Configuro el sensor de temperatura

var thermometer = new five.Thermometer({

controller: "DS18B20",

pin: 2,

board: this.byId("nano")

});

var gps = new five.GPS({

pins: {

rx: 15,

tx: 14,

board: this.byId("mega")

}

});

// si latitud o longitud cambian

gps.on("ready", function () {

console.log("position");

console.log(" latitude : ", this.latitude);

console.log(" longitude : ", this.longitude);

console.log(" altitude : ", this.altitude);

connection((db) => {

db.collection('gps')

.insert({ "latitude": this.latitude, "longitude": this.longitude, "altitude": this.altitude, "fecha": new Date() })

.then((muestrasGPS) => {

console.log('Insertando muestra GPS');

})

.catch((err) => {

console.log('Error al insertar GPS');

});

});

});

// If speed, course change log it

gps.on("navigation", function () {

console.log("navigation");

console.log(" speed : ", this.speed);

console.log(" course : ", this.course);

connection((db) => {

db.collection('navegacion')

.insert({ "velocidad": this.speed, "curso": this.course, "fecha": new Date() })

.then((muestrasGPS) => {

console.log('Insertando muestra navegacion');

})

.catch((err) => {

console.log('Error al insertar GPS');

});

});

});

//Configuro el sensor de proximidad en el pin 22

var proximityAdelante = new five.Proximity({

controller: "HCSR04",

pin: 22,

board: this.byId("mega")

});

var proximityDerecho = new five.Proximity({

controller: "HCSR04",

pin: 24,

board: this.byId("mega")

});

var proximityIzquierdo = new five.Proximity({

controller: "HCSR04",

pin: 26,

board: this.byId("mega")

});

var distanciaAdelante = 0;

motor1 = new five.Motor({

pins: {

pwm: 10,

dir: 7,

cdir: 6,

board: this.byId("mega")

}

});

motor2 = new five.Motor({

pins: {

pwm: 11,

dir: 8,

cdir: 9,

board: this.byId("mega")

}

});

motor3 = new five.Motor({

pins: {

pwm: 13,

dir: 5,

cdir: 4,

board: this.byId("mega")

}

});

motor4 = new five.Motor({

pins: {

pwm: 12,

dir: 2,

cdir: 3,

board: this.byId("mega")

}

});

function stop() {

motor1.stop();

motor2.stop();

motor3.stop();

motor4.stop();

}

//Muestro la temperatura

thermometer.on("change", function () {

//console.log(this.celsius + "°C");

//Agregado para generar hora

var ahora = new Date();

var hora = ahora.getHours() + ':' + ahora.getMinutes() + ':' + ahora.getSeconds();

var fechaAlmacenar = ahora.getFullYear() + '/' + (ahora.getMonth() + 1) + '/' + ahora.getDate();

connection((db) => {

db.collection('temperaturas')

.insert({ "valor": this.celsius, "fecha": fechaAlmacenar, "hora": hora, "fechaSys": ahora })

.then((temperaturas) => {

console.log('Insertando temperatura:' + this.celsius);

db.close();

})

.catch((err) => {

console.log('Error al insertar');

});

});

});

sensor.on("change", function (value) {

connection((db) => {

var ahora = new Date();

hora = ahora.getHours() + ':' + ahora.getMinutes() + ':' + ahora.getSeconds();

db.collection('monoxidos')

.insert({ "valor": sensor.scaleTo([20, 2000]), "fecha": new Date(), "hora": hora })

.then((sensorMQ7) => {

console.log('Insertando MQ7');

console.log(sensor.scaleTo([20, 2000]) + 'ppm'); // float

db.close();

})

.catch((err) => {

console.log('Error al insertar valores de mq7');

});

});

});

// Si se generan modificaciones en la distancia de objetos, paran o avanzan los motores

proximityAdelante.on("change", function () {

if (proximityAdelante.cm <= MINIMODISTANCIA) {

stop();

}

});

router.get('/arriba', (req, res) => {

console.log('Accionando arriba');

if (proximityAdelante.cm > MINIMODISTANCIA) {

motor1.forward(255);

motor2.forward(255);

motor3.forward(255);

motor4.forward(255);

res.json("ok");

} else {

res.json("{'error':'objeto adelante'}");

}

});

router.get('/izquierda', (req, res) => {

console.log('Accionando izquierda');

res.json("ok");

motor1.forward(255);

motor2.reverse(255);

motor3.forward(255);

motor4.reverse(255);

});

router.get('/derecha', (req, res) => {

console.log('Accionando derecha');

motor1.reverse(255);

motor2.forward(255);

motor3.reverse(255);

motor4.forward(255);

res.json("ok");

});

router.get('/abajo', (req, res) => {

console.log('Accionando abajo');

motor1.reverse(255);

motor2.reverse(255);

motor3.reverse(255);

motor4.reverse(255);

res.json("ok");

});

router.get('/stop', (req, res) => {

console.log('deteniendo');

motor1.stop();

motor2.stop();

motor3.stop();

motor4.stop();

res.json("ok");

});

router.get('/ultrasonido', (req, res) => {

res.json([{ ultrasonidoAdelante: proximityAdelante.cm },

{ ultrasonidoDerecho: proximityDerecho.cm },

{ ultrasonidoIzquierdo: proximityIzquierdo.cm }

]);

});

router.get('/gps', (req, res) => {

res.json({

latitud: gps.latitude,

longitud: gps.longitude,

altitud: gps.altitude,

velocidad: gps.speed,

sat: gps.sat,

curso: gps.course,

tiempo: gps.time

});

});

router.get('/temperatura', (req, res) => {

res.json({

temperatura: thermometer.celsius, unidad: "celsius"

});

});

router.get('/monoxido', (req, res) => {

res.json({ monoxido: sensor.scaleTo([20, 2000]), unidad: "ppm" });

});

});

module.exports = router;

### Código de Apagar y reiniciar (apagar.js)

// Require child_process

var exec = require('child_process').exec;

// Create shutdown function

var os = require('os');

var apagar = function shutdown() {

if (os.type()[0] === 'W' || os.type()[0] === 'w') {

console.log('Es windows');

} else {

console.log('Es linux');

}

console.log(os.type());

exec('shutdown -h now', function (error, stdout, stderr) { console.log(stdout); });

}

var reiniciar = function reiniciar() {

exec('shutdown -r now', function (error, stdout, stderr) { console.log(stdout); });

}

var saludar = function saludar(callback) {

console.log('Hola desde apagar.js');

}

module.exports.reiniciar = reiniciar;

module.exports.apagar = apagar;

module.exports.saludar = saludar;

## Códigos del lado del cliente

### Código de Servicio Angular (servicio.ts)

import { Gps } from './Gps';

import { Injectable } from '@angular/core';

import { Http, Headers, RequestOptions } from '@angular/http';

import {HttpClient} from '@angular/common/http';

import 'rxjs/add/operator/map';

import { Observable } from 'rxjs/Observable';

import { AppComponent } from './app.component';

import { Temperatura } from './Temperatura';

import { Sensores } from './Sensores';

import { GraficaTemperatura } from './graficaTemperatura';

import { Monoxido } from './Monoxido';

@Injectable()

export class ServicioAplicacion {

public sensores: Sensores;

constructor(public http: Http, public http2: HttpClient, public app: AppComponent) {

this.sensores = new Sensores();

}

/**

* Evento que sirve para enviar desde el componente

* @param url Url a enviar el evento [arriba, abajo, izquierda, derecha]

*/

enviarEvento(accion: String): Observable <any> {

return this.http.get(this.app.rutaBasica + accion);

}

solicitarTemperaturaActual(): Observable <Temperatura> {

return this.http.get(this.app.rutaBasica + 'temperatura')

.map(res => res.json());

}

/**

* Devuelve ([{ultrasonidoAdelante:proximityAdelante.cm},

{ultrasonidoDerecho: proximityDerecho.cm},

{ultrasonidoIzquierdo: proximityIzquierdo.cm}

])

*/

solicitarUltrasonidosActual(): Observable <any> {

return this.http.get(this.app.rutaBasica + 'ultrasonido')

.map(res => res.json());

}

/**devuelve

* {monoxido: sensor.scaleTo([20,2000]), unidad: "ppm"}

*/

solicitarMonoxidoActual(): Observable <any> {

return this.http.get(this.app.rutaBasica + 'monoxido')

.map(res => res.json());

}

solicitarGpsActual(): Observable <Gps> {

return this.http.get(this.app.rutaBasica + 'gps')

.map(res => res.json());

}

pedirImagen(): Observable<boolean> {

return this.http.get(this.app.rutaWeb)

.map(res => res.json());

}

actualizarValores(muestraSensores: Sensores) {

this.sensores = muestraSensores;

}

apagar() {

return this.http.get(this.app.rutaBasica + 'apagar');

}

reiniciar() {

return this.http.get(this.app.rutaBasica + 'reiniciar');

}

solicitarTodasTemperaturas(): Observable <GraficaTemperatura[]> {

return this.http2.get<GraficaTemperatura[]>(this.app.rutaBasica + 'temperaturas');

}

solicitarMonoxidoActualBD(): Observable <Monoxido> {

return this.http2.get<Monoxido>(this.app.rutaBasica + 'monoxidosActual');

}

}

### Código de appComponent.ts Angular

import { Sensores } from './Sensores';

import { Component } from '@angular/core';

import { TemperaturaService } from './temperatura.service';

import { Temperatura } from './Temperatura';

import { DatePipe } from '@angular/common';

@Component({

selector: 'app-root',

templateUrl: './app.component.html',

styleUrls: ['./app.component.css'],

providers: [TemperaturaService],

})

export class AppComponent {

titulo = 'Sistema Autónomo Robótico';

public temperaturas: Temperatura[];

public sensoresActuales: Sensores;

public tiempoDelay;

public mensaje = '';

public rutaBasica = 'http://192.168.2.1:3000/api/';

// public rutaBasica = 'http://localhost:3000/api/';

// public rutaBasica = 'http://192.168.1.39:3000/api/';

public rutaWeb = 'http://192.168.2.1:8081';

constructor(public service: TemperaturaService) {

this.sensoresActuales = new Sensores();

this.tiempoDelay = 1000;

}

}

### Código de appModule (rutas) [Extracto]

const routes: Routes = [

{ path: '', component: PizarraComponent },

{ path: 'estadisticas', component: EstadisticasComponent },

{ path: 'control', component: PanelInferiorComponent }

];

@NgModule({

declarations: [

AppComponent,

CapturaVideoComponent,

TablaSensoresComponent,

TablaInfoComponent,

PanelInferiorComponent,

PanelControlComponent,

PizarraComponent,

EstadisticasComponent,

EncabezadoComponent,

],

imports: [

BrowserModule,

HttpModule,

RouterModule.forRoot(routes),

NgxChartsModule,

BrowserAnimationsModule,

FormsModule,

HttpClientModule

],

providers: [TemperaturaService],

bootstrap: [AppComponent]

})

export class AppModule { }

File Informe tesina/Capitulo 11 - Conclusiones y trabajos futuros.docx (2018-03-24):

# Capítulo 11 – Conclusión y trabajos futuros

En este capítulo se detallarán las conclusiones en base a los objetivos generales y específicos planteados para el desarrollo de la tesina. A su vez, se describirán trabajos futuros.

## 11.1 Conclusión final

Revisando el objetivo general y los diversos objetivos específicos, tratados al principio de esta tesina (referencia cap1), se llega a las siguientes conclusiones.

Se desarrolló un prototipo de un Sistema Autónomo Robótico (SAR), gestionado por un software definido como agente inteligente (que responde al modelo basado en objetivos) para la exploración y análisis del medio ambiente.

Mediante la experiencia adquirida al trabajar en establecimientos educativos en áreas relacionadas con la robótica, y todas las investigaciones y ensayos realizados para producir este prototipo, podemos concluir que el mismo sirve de base o modelo para el desarrollo de proyectos a fines.

### 11.1.1 Ensamblar un robot móvil integrando las plataformas Arduino y Raspberry Pi con diversos módulos y software.

Se investigaron variadas tecnologías, que permiten la integración de estas plataformas fundamentales para el ensamblado del robot móvil. En base a esta investigación, podemos concluir que la interacción entre la Rasperry Pi y Arduino es viable, dado los diferentes módulos y componentes compatibles a nivel hardware y los protocolos de comunicación a nivel software.

### 11.1.2 Desarrollar una aplicación web multiplataforma que mediante comunicación inalámbrica permita el control del Robot móvil.

Una de las principales características de las aplicaciones web, para el desarrollo de aplicaciones móviles, es la de permitir su utilización en distintos sistemas operativos y plataformas hardware. Esto permite que la aplicación cliente, ejecutada por un navegador web, sea multiplataforma. Como consecuencia, existen diversos clientes, que se conectan de forma inalámbrica al SAR. Estos clientes pueden ejecutar acciones sobre el robot móvil.

El desarrollo del software del SAR basado en la arquitectura cliente/servidor y enfocado en el modelo frontend/backend, generó múltiples beneficios en cuanto a las características del software, como la interoperabilidad, reutilización, portabilidad, flexibilidad, extensibilidad y escalabilidad.

Podemos concluir, que además de los beneficios mencionados, el tiempo de desarrollo de la aplicación fue menor a lo proyectado.

### 11.1.3 Investigar protocolos existentes y evaluar la necesidad de diseño de protocolos de comunicación para el control y procesamiento de datos entre el microcontrolador y la aplicación.

A partir de la investigación de distintos protocolos de comunicación entre las plataformas utilizadas en el desarrollo de esta tesina, se identificó uno en particular, denominado Firmata, que nos permitió realizar dicha comunicación.

La ventaja primordial de la utilización de Firmata es que se encuentra ampliamente utilizado, razón por la cual, es compatible con múltiples librerías y lenguajes de programación. A su vez, queda claro que gracias a su existencia y lo expresado anteriormente no fue necesario el desarrollo de un nuevo protocolo que cumpla la misma función.

### 11.1.4 Ensamblar físicamente e integrar a nivel de software los distintos componentes (sensores y actuadores) al SAR.

Gracias a la utilización de la plataforma Arduino y su compatibilidad (mencionada en el cap3) con sensores y actuadores, es que la integración física de los elementos que componen el SAR, no fue una actividad tediosa. Esto es así, porque, tanto la plataforma como los componentes, nacen con la idea de poder generar soluciones a implementaciones electrónicas o proyectos a fines, sin la necesidad de conocimientos técnicos previos.

### 11.1.5 Extender la aplicación para interactuar con la información que brinda el SAR de los sensores.

Para el almacenamiento de los valores obtenidos por los sensores que componen al SAR, se utilizó un sistema de bases de datos (Mongo cap5). Este sistema facilitó el procesamiento de datos.

Por otro lado, con la implementación de una API REST, se simplificó la generación y representación de estadísticas. A su vez, esta API permitió el flujo de datos en tiempo real, de los eventos y los valores sensados.

## 11.2 Trabajos futuros

Se proponen como líneas futuras de mejoras, para el SAR, las que se detallan a continuación:

- En cuanto la estructura, se propone mejorarla para adaptarla a distintos ambientes.
- Incorporar nuevos sensores y actuadores, como por ejemplo servo motores, sensor de humedad, sensor impacto, acelerómetro, sensor de llamas, etc., permitiendo así mejorar el reconocimiento del entorno en el que se encuentre el SAR.
- Extender la aplicación para generar mayor cantidad de estadísticas, que permitan comprender con mejor precisión el ambiente que lo rodee y así tomar decisiones que controlen su flujo de acciones.
- Generar un diseño monolítico, que permita generar independencia entre la unidad lógica y física. De tal forma que se logre un bajo acoplamiento.

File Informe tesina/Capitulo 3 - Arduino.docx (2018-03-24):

# Capítulo 3 – Arduino

En este capítulo conoceremos qué es la plataforma Arduino, sus comienzos y otras tecnologías que colaboraron en el desarrollo de la misma. Además, analizaremos características de la placa, examinando capacidades técnicas como el microcontrolador, memoria y medios de comunicación.

También veremos el abanico de placas producidas por la compañía, sus especificaciones técnicas, similitudes y diferencias. Por otro lado, se examinarán diversos sensores, actuadores y módulos compatibles con la plataforma Arduino. Por último, se comentará la aplicación en las instituciones educativas y la utilización de Arduino en el SAR.

## 3.1 Arduino

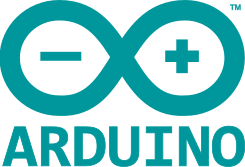
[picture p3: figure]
Arduino Logo.svg

Arduino es una plataforma y compañía, del mismo nombre, de electrónica "open-source" o de código abierto cuyo objetivo es brindar hardware y software de fácil utilización. Es decir, se propone como una plataforma sencilla con una curva de aprendizaje baja para realizar proyectos interactivos para público no necesariamente con conocimientos técnicos.

Ilustración 1 - Logo Arduino

Arduino se trata de una SBC (AGREGAR REFERENCIA CAPITULO 2.4) con entradas y salidas, analógicas y digitales, la cual es programada bajo un entorno de desarrollo, basado en el entorno de programación inspirado en Processing y en la estructura de programación Wiring. En la imagen (Ilustración 1 - Logo Arduino - Logo Arduino) se puede ver el logo oficial de la compañía.

## 3.2 Historia

Arduino se inició en el año 2005 como un proyecto para estudiantes en el Instituto IVREA, en Ivrea (Italia). Dado que se utilizaba el microcontrolador BASIC Stamp, cuyo costo era alto para para los fines educativos se comienza el proyecto Arduino. El nombre del proyecto viene del nombre del Bar di Re Arduino (Bar del Rey Arduino), donde Massimo Banzi empezaba a desarrollarlo. [1]

Un estudiante, Hernando Barragán, quien desarrolló la tarjeta electrónica Wiring, el lenguaje de programación y la plataforma de desarrollo. Una vez concluida dicha plataforma, los investigadores trabajaron para hacerlo más ligero, más económico y de mayor alcance a la comunidad de hardware y código abierto.

Posteriormente, Google colaboró en el desarrollo del Kit Android ADK (Accesory Development Kit), una placa Arduino capaz de comunicarse directamente con teléfonos móviles inteligentes bajo el sistema operativo Android para que el teléfono controle luces, motores y sensores conectados a Arduino.

Para la producción en serie de la primera versión se tomó en cuenta que el coste no fuera mayor de 30 euros, que fuera ensamblado en una placa de color azul, debía ser Plug and Play y que trabajara con todas las plataformas informáticas tales como MacOSX, Windows y GNU/Linux.

### 3.2.1 Wiring

Wiring es una plataforma de prototipado electrónico de fuente abierta compuesta de un lenguaje de programación, un entorno de desarrollo integrado (IDE), y un microcontrolador.

Esta plataforma permite escribir software para controlar dispositivos conectados a la tarjeta electrónica para crear toda clase de objetos interactivos, espacios o experiencias físicas que sienten y responden al mundo físico.

Este proceso se llama sketching con hardware; se explora una gran cantidad de ideas de forma muy rápida, se seleccionan las más interesantes, se afinan y producen prototipos en un proceso iterativo.

Wiring toma de Processing la IDE y el concepto de sketch, pero enfocado en la programación de microcontroladores en vez de programación gráfica. Provee una librería de C/C++ la cual simplifica operaciones comunes como el manejo de entrada/salida. Los programas de Wiring están escritos en C/C++, pese a que sus usuarios sólo necesiten definir dos funciones para hacer un programa ejecutable:

setup() – una función ejecutada sólo una vez en el arranque de la placa, la cual puede ser usada para definir los ajustes iniciales de un entorno.

loop() – una función llamada repetidamente hasta que la placa es apagada.

Como podemos apreciar en la siguiente ilustración (Ilustración 2 – Código de Blink en Wiring IDE) hacer un blink a un led es muy sencillo dado la abstracción que nos otorga la librería. Un blink es un parpadeo de un led conectado a la placa. Se lo considera el “hola mundo” de Arduino.

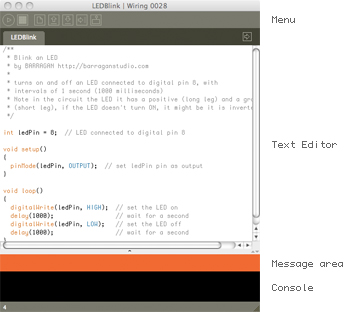
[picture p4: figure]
IDE screenshot

Ilustración 2 – Código de Blink en Wiring IDE

Para ejemplificar la interfase de programación que poreve Wiring al usuario en contrasposición a la utilización de la API del fabricante pude obserbarse un como ejmplo el código (Ilustración 3 - C++ Blink ejemplo) puede ser escrito como Ilustración 2 - Wiring IDE[^1]

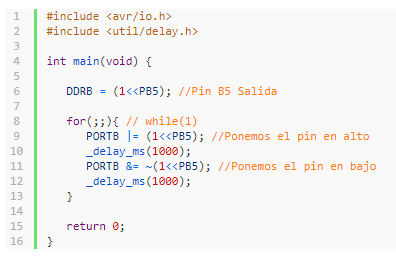
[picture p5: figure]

Ilustración 3 - C++ Blink ejemplo

### 3.2.2 Processing

Es un lenguaje de programación y entorno de desarrollo integrado de código abierto basado en Java, de fácil utilización, y que sirve como medio para la enseñanza y producción de proyectos multimedia e interactivos de diseño digital. En la imagen (Ilustración 4 - Logo de Processing) se puede apreciar su logo.

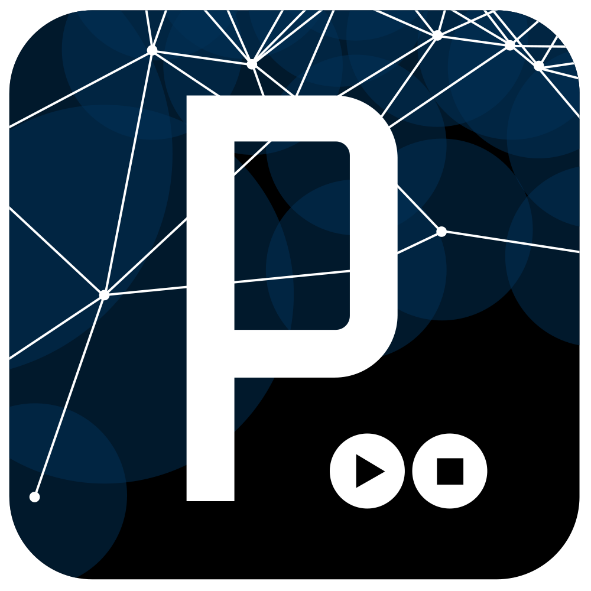
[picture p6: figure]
Resultado de imagen para processing logo

Uno de los objetivos expresos de Processing es el de actuar como herramienta para que artistas, diseñadores visuales y miembros de otras comunidades ajenos a la programación, aprendan las bases de la misma a través de una realimentación gráfica inmediata y visual de los resultados obtenidos de su experiencia de programación.

El lenguaje de Processing se basa en Java, aunque hace uso de una sintaxis simplificada y de una biblioteca sencilla para generación de gráficos.

Ilustración 4 - Logo de Processing

Más adelante podemos apreciar un extracto de código de Processing viendo la similitud con el código Arduino. Al correr este ejemplo podemos observar como renderiza visualmente el código en el visor (Ilustración 5 - Processing ejemplo)

void setup() {

size(480, 120);

}

void draw() {

if (mousePressed) {

fill(0);

} else {

fill(255);

}

ellipse(mouseX, mouseY, 80, 80);

}

Ilustración 5 - Processing ejemplo

### 3.2.3 Fritzing

El entorno de software Fritzing ayuda a los diseñadores y artistas a documentar sus prototipos interactivos y dar paso en la creación de prototipos físicos al producto real. Como podemos apreciar en la siguiente ilustración (Ilustración 6 - Entorno Fritzing), permite arrastrar componentes y generar un sketch. Fritzing es creado bajo los principios de Processing y Arduino, y permite a los usuarios a documentar sus prototipos basados en Arduino y crear esquemas de circuitos impresos para su posterior fabricación

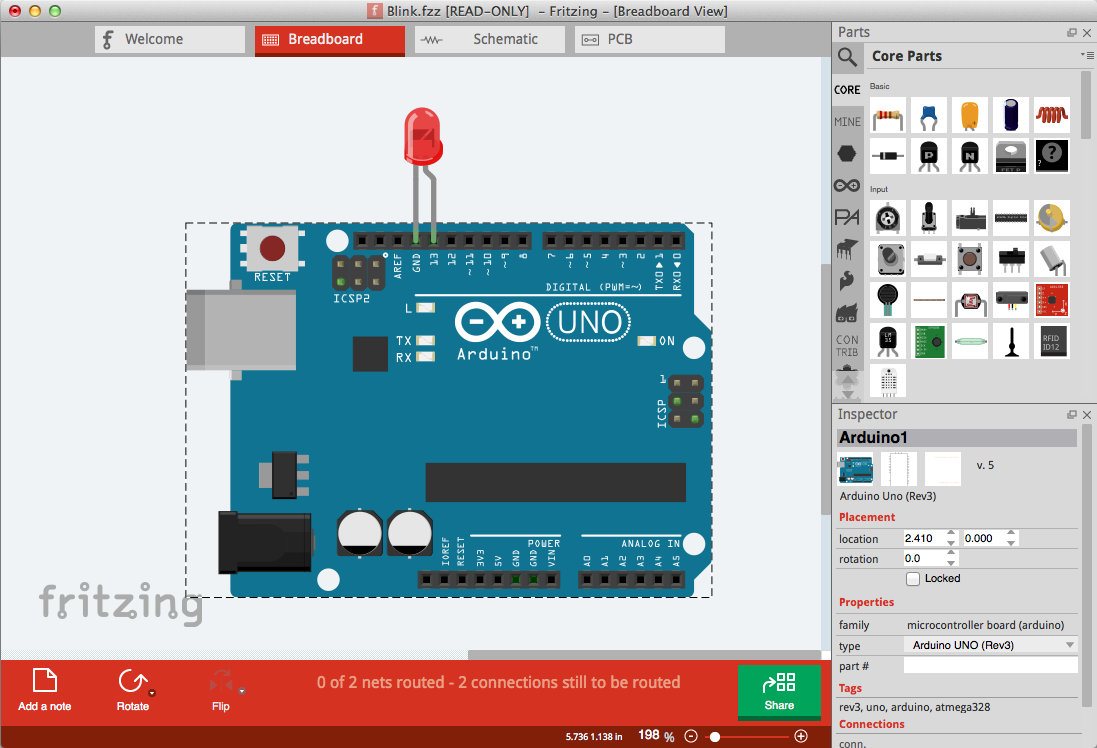
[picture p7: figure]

Ilustración 6 - Entorno Fritzing

## 3.3 Características generales de la plataforma

- Arduino es una plataforma de hardware libre, basada en una placa con un microcontrolador y un entorno de desarrollo, diseñada para facilitar el uso de la electrónica en proyectos multidisciplinares.
- Arduino es una plataforma de hardware abierto que facilita la programación de un microcontrolador. Los microcontroladores nos rodean en nuestra vida diaria, usan los sensores para ecuchar el mundo físico y los actuadores para interactuar con el mismo. Los microcontroladores leen sobre los sensores y escriben sobre los actuadores.

La plataforma consiste en una placa de circuito impreso con un microcontrolador, usualmente Atmel AVR, puertos digitales y analógicos de entrada/salida los cuales pueden conectarse a placas de expansión (shields), que amplían las características de funcionamiento de la placa Arduino. Asimismo, posee un puerto de conexión USB desde donde se puede alimentar la placa y establecer comunicación con el computador.

Las placas Arduino además incluyen puertos serie, uno de ellos asociado a la conexión USB a la computadora a través de una UART (Glosario) .

Por otro lado, también opera en nivel TTL (transistor-transistor logic). Esto significa que la comunicación se realiza mediante variaciones en la señal entre 0V y Vcc (donde Vcc suele ser 3.3V o 5V). Por el contrario, otros sistemas de transmisión emplean variaciones de voltaje de -Vcc a +Vcc (por ejemplo, los puertos RS-232 típicamente varían entre -13V a 13V).

Como podemos observar en la siguiente ilustración (Ilustración 7 - Ejemplo serie), se realiza una comunicación serie a (9600 bps) imprimiendo un contador. La zona marcada con rojo, es un botón que al presionarlo nos permite acceder a la terminal y ver el flujo serie seteando el clock correspondiente.

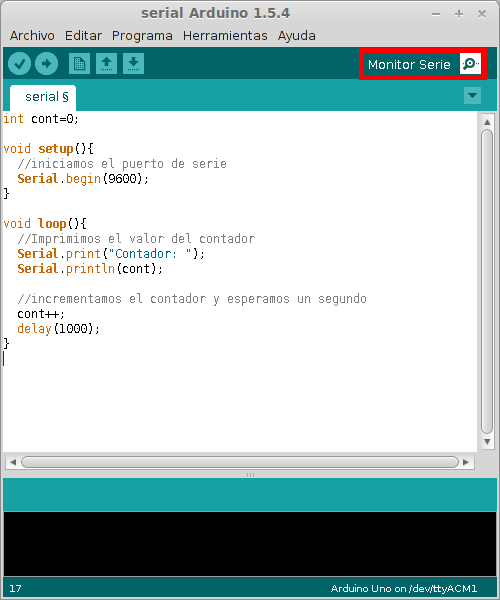
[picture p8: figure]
arduino-serial-monitor-IDE

Ilustración 7 - Ejemplo serie

## 3.4 Distintas plataformas para Arduino

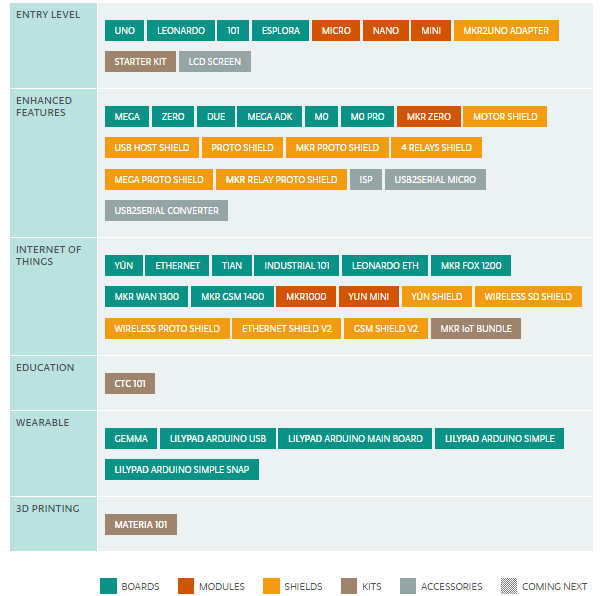
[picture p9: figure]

Ilustración 8 - Niveles de entrada a la plataforma Arduino

Existe una gran variedad de productos Arduino, la compañía los cataloga, como se puede aprecias en (Ilustración 8 - Niveles de entrada a la plataforma Arduino), en distintos niveles según su utilidad[^2]:

- Nivel de entrada: Son los más sencillos de utilizar, ideales para comenzar con la plataforma Arduino y realizar proyectos sencillos.
- Características mejoradas: Estas plataformas poseen características superiores, con respecto a las del nivel de entrada, están pensadas para proyectos más avanzados o de respuesta más rápida.
- Internet de las cosas: Estas placas vienen incorporadas con componentes que permitan realizar trabajos relacionados con la IoT (Internet de las cosas Glosario) mediante la incorporación de hardware de conectividad.
- Educación: En este caso, Arduino, ofrece un kit con herramientas y más de 25 proyectos, orientados a la educación, para realizar con sus plataformas.
- Usables: Estas plataformas están pensadas para “agregarle algo de electrónica” a prendas de vestir.
- Impresión 3D: Arduino ofrece una impresora 3D nombrada como Materia 101.

El hardware Arduino más sencillo consiste en una placa con un microcontrolador y una serie de puertos de entrada y salida. Los microcontroladores de 8 bits de AVR más utilizados en estas placas son el Atmega168, Atmega328, Atmega1280, y Atmega8 por su sencillez y bajo coste, aunque también se dispone de microcontroladores ARM, cómo el caso del CortexM3 de 32 bits. A pesar de que ARM y AVR son plataformas diferentes, al utilizar la IDE de Arduino, los programas se compilan y luego se ejecutan sin cambios en cualquiera de las plataformas. En la imagen (Ilustración 9 - Arduino Uno) se visualiza la distribución física de puertos y componentes de la versión Arduino Uno R3.

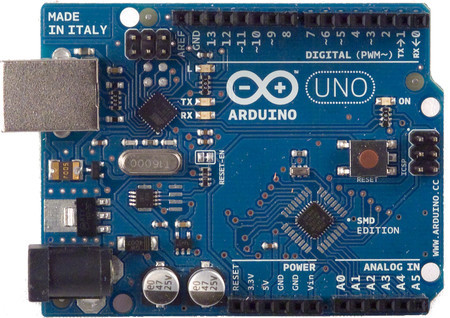
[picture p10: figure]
Arduino UNO R3

Ilustración 9 - Arduino Uno

Una primera diferenciación entre los distintos modelos de Arduino la encontraremos en el voltaje o tensión de alimentación de las placas. Las basadas en CortexM3 operan con un voltaje de 3,3 voltios, mientras que la mayor parte de las placas basadas en AVR utilizan una tensión de 5 voltios. Esto de todas formas no es un factor decisivo en la elección de una placa, dado que existen conmutadores de tensión en muchos actuadores y sensores compatibles.

## 3.5 Aplicaciones

Los usos posibles que se le pueden dar a “un Arduino”, en forma general son:

- Utilizarlo como microcontrolador, con un programa descargado desde un ordenador y funcionamiento de forma independiente, recibiendo entradas de sensores y realizando acciones sobre actuadores en función de las entradas y el programa.
- Idem anterior pero conectado a un ordenador (que también podría ser un SBC como Raspberry Pi).

Enumerarenmos ahora una serie de razones de utilización

## 3.6 Motivaciones para su uso

### 3.6.1 La comunidad

Arduino cuenta con una gran comunidad, cuayas actividades se centran en la experimentación, publicación de resultados y proyectos, y orgnzación de eventos. El manifiesto de la comunidad Arduino dice (traducción al español):

“Apoyar al ecosistema de hardware y software de open source Arduino, haciendo que los productos electrónicos sean abiertos y participativos.

Servir como un evangelizador para Arduino, expandir el ecosistema de código abierto a estudiantes, fabricantes, desarrolladores, diseñadores, ingenieros y empresas dentro de sus comunidades locales.

Construir una red global de comunidades que diseñen y codifiquen proyectos, intercambien ideas, organicen actividades de colaboración y dicten cursos oficiales de Arduino, independientemente de su edad, sexo, idioma y capacidad técnica”[^3]

Dentro de la página oficial se brinda soporte por medio de documentación, foros y la publicación de un blog con novedades y proyectos relevantes que se encuentran en desarrollo.

Además, se han creado sitios como Arduino Playground (http://playground.arduino.cc/) que consiste en una Wiki donde todos los usuarios de Arduino pueden contribuir. Es el lugar donde publicar y compartir código, diagramas de circuitos, guías, manuales, cursos. Es una de las base de datos de conocimiento de la comunidad de Arduino. Este sitio a su vez tiene soporte de distintos lenguajes como el español (https://playground.arduino.cc/Es/Es).

Otro ejemplo de las actividades de la comunidad es el sitio Arduino Hub, un lugar donde se comparten los proyectos, dando los distintos pasos para reproducirlo.

El Arduino day, o cumpleaños de Arduino, es una celebración mundial que se lleva a cabo una vez al año en diversos puntos del mundo. Este evento es organizado por la comunidad de Arduino y/o sus fundadores. En él se desarrollan diferentes talleres, charlas y concursos, entre otras actividades, relacionadas con la plataforma.

La siguiente imagen (Ilustración 10 - Logotipo comunidad open-source de Arduino) muestra el logotipo oficial de la comunidad open-source de Arduino.

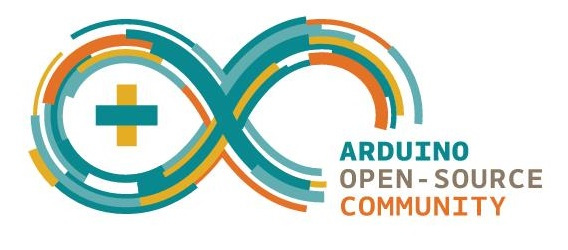
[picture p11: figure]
ArduinoCommunityLogo_EPS

Ilustración 10 - Logotipo comunidad open-source de Arduino

### 3.6.2 Sencillez de programación

Gracias a la reutilización de las ideas de Wiring, Arduino provee un alto nivel de abstracción con respecto al hardware.

Por ejemplo, para establecer como salida los los puertos 1 al 7, se puede utilizar el siguiente fragmento de código:

PinMode(1,OUTPUT) ;

PinMode(2,OUTPUT) ;

…;

PinMode(7,OUTPUT) ;

en contraposiciic con:

DDRD = B11111110; [^4] // sets Arduino pins 1 to 7 as outputs, pin 0 as input

### 3.6.3 Hardware económico

Lo único que “vale” en la placa son sus componentes, ya que no debemos pagar el costo de la licencia de su creador, por el hecho de ser hardware libre.

## 3.7 Incorporación de Arduino en las escuelas

Las deviersas características y motivaciones hacen atractiva a la plataforma Arduino para su incorporación en las escuelas.

Esto ha llevado la

creación de proyectos articulares entre distintos espacios curriculares.

Dentro de las principales características que han promovido esta tendencia sen encuentran la sencillez del lenguaje de programación que permite que alumnos y docentes no necesariamente del ámbito de la informática y la electrónica pueden utilizarlo, contribuyendo a la construcción colectiva del conocimiento, promoviendo la interdisciplinariedad escolar, permitiendo la colaboración de docentes de distintas áreas cooperar en la articulación de proyectos.

Desde el punto de vista pedagógico del proceso de aprendizaje , este tipo de actividades permiten al sujeto que aprende ser participante activo, desde la concepción de la idea hasta el producto final, incorporando gradualmente conocimientos técnicos específicos.

Este tipo de actividades educativas hacen que la tecnología y su uso se pongan al servicio de la creatividad, el juego, la experimentación y la invención, con la posibilidad de ser adaptado al contexto en el que se inserta. Además, proporcionar la recuperación de la tecnología obsoleta existente en ellas como se describe en la siguiente sección.

### 3.7.1 Las tres erres

Las tres erres (reducir, reutilizar, reciclar) es una regla para cuidar el medio ambiente, específicamente para reducir el volumen de residuos o basura generada.

Cuando hablamos de reducir lo que estamos diciendo es que se debe tratar de simplificar el consumo de los productos directos.

Al decir reutilizar, nos estamos refiriendo a poder volver a utilizar los objetos y darles la mayor utilidad posible antes de que llegue el momento de desecharlos.

Por otro lado, reciclar consiste en el proceso de someter los materiales a una transformación en el cual se puedan volver a utilizar.

Esta definición se pretende aplicar en las escuelas haciendo un proceso de clasificación, selección y desoldando componentes electrónicos de placas en desuso y materiales que se han desechado en las instituciones o en hogares de los alumnos.

## 3.8 Actuadores y sensores

Un actuador es un dispositivo capaz de transformar energía hidráulica, neumática o eléctrica en la activación de una acción con la finalidad de generar un efecto sobre un proceso automatizado. Este recibe la orden de un regulador o controlador y en función a ella genera la orden para activar un elemento final de control, como por ejemplo un LED.

Por otro lado, un sensor es un objeto capaz de detectar magnitudes físicas o químicas, llamadas variables de instrumentación, y transformarlas en variables eléctricas. Las variables de instrumentación pueden ser, por ejemplo: intensidad lumínica, temperatura, distancia, aceleración, inclinación, presión, desplazamiento, fuerza, torsión, humedad, movimiento, pH, etc.

En conjunto, los sensores y actuadores, permiten la creación de distintos tipos de artefactos, que posibilitan comunicarse con el ambiente que los rodea, modificándolo (actuadores) o recibir estímulos (sensores).

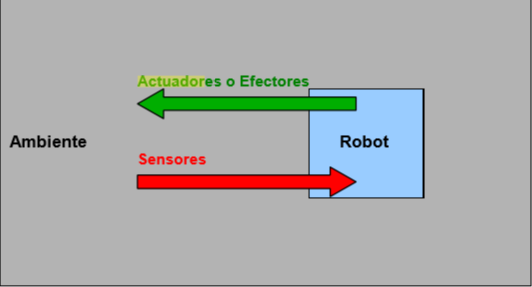
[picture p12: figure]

Ilustración 11- Representación actuadores y sensores

En esta imagen (Ilustración 11- Representación actuadores y sensores) se representan los datos que un robot puede capturar de su ambiente por medio de diversos sensores, y a su vez como podría interactuar con el mismo mediante actuadores.

## 3.9 Actuadores en el SAR

La electrónica industrial ha generado estandarización en el campo de los sensores y actuadores, muchos de estos últimos con buen soporte en Arduino. Precisamente en el SAR se utilizarán:

- Motores de corriente continua
  - Para el desplazamiento del robot móvil
- LED
  - Para indicar estados del RM

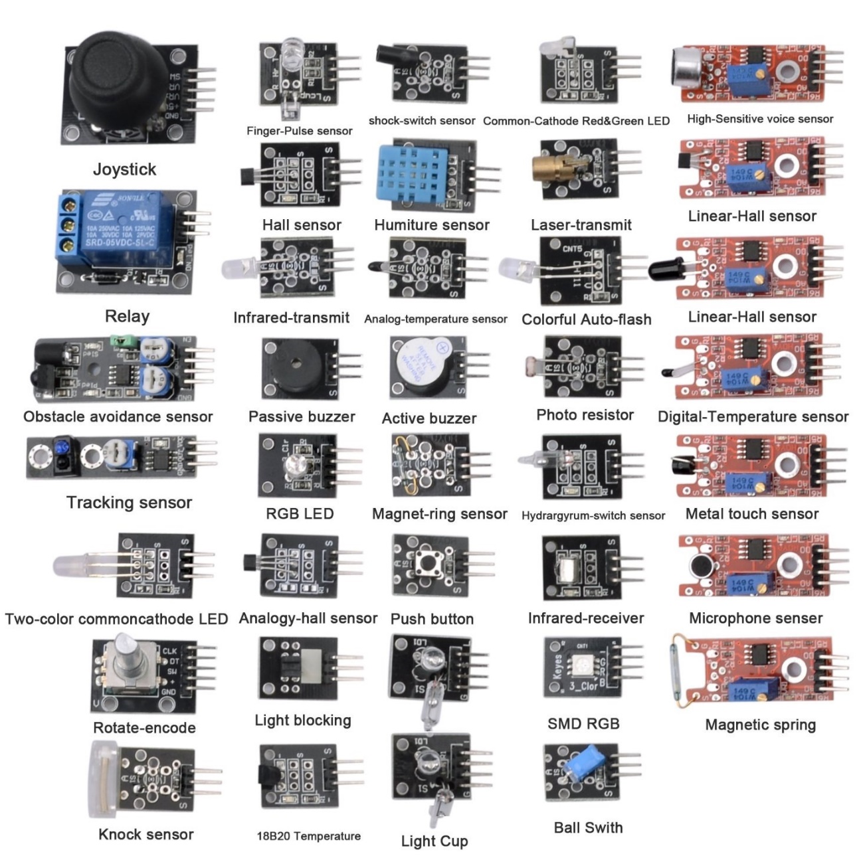
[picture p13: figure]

Ilustración 12 - Actuadores y sensores compatibles con Arduino

## 3.10 Sensores en el SAR

El SAR utiliza los siguientes sensores:

- Sensor ultrasónico HC-SR04
  - Para detectar objetos, y distancia entre el RM y elementos del ambiente
- Sensor de Temperatura KY-001
  - Incorporado para analizar la temperatura del ambiente
- Sensor de presencia de gases MQ-7
  - Detección de monóxido de carbono

Algunos de los sensores y actuadores se pueden apreciar en la ilustración anterior (Ilustración 12 - Actuadores y sensores compatibles con Arduino).

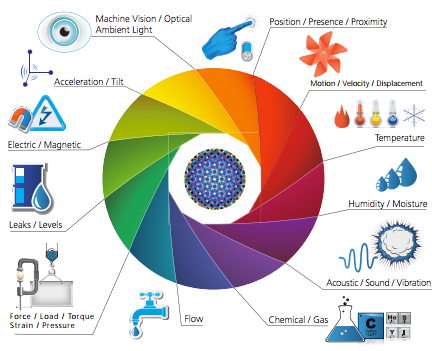
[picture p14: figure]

Ilustración 13- Representación de sensores

En esta imagen (Ilustración 13- Representación de sensores) se pueden apreciar los distintos factores de un entorno que pueden ser evaluadores con sensores mencionados anteriormente.

## 3.11 Módulos o shields en el SAR

El SAR utiliza[^5]:

- MotorShield L298
  - Para administración del puente H y gestión de los motores de CC
- Módulo bluetooth HC-05
  - Para la comunicación con dispositivos compatibles (móviles y/o computadoras)
  - Envío de órdenes
- Módulo GPS NEO-6
  - Para la geolocalización del RM
- Módulo ESP8266
  - Conectividad y transferencia de datos vía WIFI
  - Activación del modo AP

A lo largo del desarrollo de la tesina se fueron implementando diversos casos de pruebas sobre los sensores, actuadores y módulos especificados en esta sección. Las pruebas se encuentran anexas en este documento.

## 3.12 Resumen

Como vimos en el presente capítulo, Arduino es una plataforma electrónica open-source, basada en una placa con un microcontrolador y un entorno de desarrollo, diseñada para facilitar el uso de la electrónica en proyectos multidisciplinares. A su vez facilita la programación de un microcontrolador, este último lee sobre los sensores y escribe sobre los actuadores.

Un actuador es un dispositivo capaz de transformar energía hidráulica, neumática o eléctrica en la activación de una acción con la finalidad de generar un efecto sobre un proceso automatizado.

Por otro lado, un sensor es un objeto capaz de detectar magnitudes físicas o químicas, llamadas variables de instrumentación, y transformarlas en variables eléctricas. Además, existen módulos que integran sensores y actuadores con un micro controlador

[^1] http://comoprogramarpic.blogspot.com.ar/2012/06/programando-un-atmel-mi-primer-programa.html
[^2] https://www.arduino.cc/en/Main/Products
[^3] https://www.arduino.cc/en/aug/
[^4] https://www.arduino.cc/en/Reference/PortManipulation
[^5] El uso de algunos de estos módulos queda en forma tentativa, dado que existen también en la Raspberry y su uso puede ser complementario.

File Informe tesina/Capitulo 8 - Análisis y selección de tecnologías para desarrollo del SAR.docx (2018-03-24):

# Capítulo 8 - Análisis y selección de tecnologías para desarrollo del SAR

En capítulos anteriores analizamos diversas tecnologías hardware y software relacionadas con la robótica. Dentro de las tecnologías hardware investigamos las plataformas Arduino (Capítulo 3 – Arduino) y Raspberry Pi (Capítulo 4 – Raspberry Pi). De las diversas herramientas en tecnologías software para aplicaciones móviles, investigamos aquellas que permiten desarrollar una aplicación que interactúe con el hardware mencionado.

En este capítulo examinamos dichas tecnologías para concluir cuales son las que integran el SAR. Para ello, realizamos diversas comparativas sobre características, ventajas y desventajas de cada una de las plataformas. Además, se presentan las problemáticas surgidas al relacionar los componentes.

## 8.1 Primer análisis

El análisis realizado de las distintas tecnologías de hardware y software, basándose en factores como rendimientos, tiempos de respuesta, consumo energético, portabilidad y compatibilidad, nos permitió seleccionar los elementos que componen el SAR.

El hardware estudiado y utilizado a lo largo del desarrollo, fue el de la familia Arduino y Raspberry Pi.

Dentro de la plataforma Arduino se probaron las versiones Arduino Uno, Arduino Mega y Arduino Nano, siendo estos dos últimos los utilizados en el SAR. Además, se experimentaron con variados módulos, sensores y actuadores compatibles con esta familia como la cámara OV7670, ESP8266, Bluetooth, DHT11, entre otros. Los ensayos realizados con estos componentes se encuentran en el anexo de casos pruebas de módulos, sensores y actuadores.

En el caso de Raspberry Pi utilizamos la versión Pi 3 modelo B, en conjunto con la cámara compatible para esta SBC.

El software investigado para el desarrollo de aplicaciones móviles fue mencionado en los capítulos 5 y 6 (Capítulo 5 - Aplicaciones Móviles y Capítulo 6 – Stack MEAN). La idea era encontrar compatibilidad entre los elementos del hardware, utilizando el software como interfaz entre ellos.

## 8.2 Selección tecnologías hardware

### 8.2.1 Arduino como controlador del SAR

Como se abordó en el capítulo 3 (Capítulo 3 – Arduino), siendo una arquitectura hardware pensada para hobbistas, diseñadores y personas no relacionadas con la electrónica ni la programación a bajo nivel, Arduino permite una curva de aprendizaje relativamente plana y la facilidad de conexión de los distintos componentes la hace muy atractiva, para encarar distintos proyectos con diversos niveles de complejidad.

Las placas Arduino, fueron pensadas mayormente para el uso del control de sensores y actuadores utilizando un microcontrolador, esto genera una mejor transición desde la electrónica discreta a la electrónica programable.

Dentro de la plataforma Arduino, se seleccionó Arduino UNO, donde se elaboraron distintos prototipos simples con protoboard, desde la manipulación de actuadores con motores hasta la toma de datos de distintos sensores como temperatura, humedad, obstáculos, entre otros. Se encontró en la placa Arduino UNO una baja disponibilidad de pines E/S para la cantidad de sensores/actuadores y módulos que se requerían conectar. Por tal motivo, se decidió ampliar la cantidad de pines optando por la placa Arduino Mega. Esta última, otorga mayor cantidad de pines, sin expandir la cantidad de memoria ni procesamiento. Este detalle devino en la dificultad a la hora de la programación, por contar con pocas interrupciones hardware, forzando a la utilización de consulta periódica o pooling en el bucle principal (loop). Estos problemas surgieron a la hora de conectar el módulo de la cámara OV7670 y el módulo WiFi ESP8266, los cuales requerían una alta cantidad de pines y nivel de cómputo.

Teniendo en cuenta el párrafo anterior, es que se optó del traspaso de una plataforma que trabaja con un microcontrolador a un computador, resultando ser la Raspberry Pi

### 8.2.2 Raspberry como administrador del SAR

En el capítulo 4 (Capítulo 4 – Raspberry Pi) se mencionó y analizó el computador de placa reducida (SBC) Raspberry Pi, en el cual se pudo apreciar las características fundamentales del mismo. Esta plataforma se diseñó, primordialmente, con fines didácticos para la educación secundaria, es por esto, que su costo es relativamente bajo. Al contar, la misma, con todas las capacidades básicas de una computadora portátil de hoy en día con su respectivo microprocesador (bastante potente para nuestras necesidades), memorias y puertos físicos (como el USB, HDMI, microSD, entre otros); y la posibilidad de instalar un sistema operativo totalmente funcional y con interfaz gráfica (en este caso Raspbian), es que se seleccionó como centro de administración y control del SAR.

Además, cuenta con pines GPIO para las conexión y manipulación de distintos módulos (como actuadores y sensores), aunque como se analiza en el apartado siguiente, se delegó en placas Arduino Mega y Arduino Nano las funcionalidades de control y sensado, exceptuando la conexión y procesamiento de imágenes, delegadas a la cámara de Raspberry Pi v2 y las comunicaciones inalámbricas proporcionadas por los módulos wifi y bluetooth integrados a este computador.

### 8.2.3 Comparativa entre Arduino Mega, Arduino Nano y Raspberry Pi 3 Model b

Factor | Arduino Mega | Arduino Nano | Raspberry Pi3 Model B
Microcontrolador/ Microprocesador | ATmega 1280 - 16Mhz 8bits | ATmega328 – 16Mhz 8bits | Quad Core 1.2GHz Broadcom BCM2837 64bit
Tensión | 5v | 5v | 5v
Memoria | 128 KB (Bootloader 4KB) | 32 KB (Bootloader 2KB) | 1 GB
Digital I/O | 54, 15 PWM | 22, 6 PWM | 40 GPIO
Analog I/O | 16 | 8
Interfaces | USB x 1(energía) | USB x 1 (energia) | USB x 4, HDMI, CSI, DSI, MicroSD, WLAN y BLE, microUSB (Energía)

Dada la comparativa entre las tecnologías, se decide utilizar las placas Arduinos para el control de módulos, sensores y actuadores. La Raspberry Pi quedó seleccionada para la captura de imágenes y como servidor dedicado. Tanto la Arduino Nano como la Mega se conectan a la Raspberry a través de sus interfaces USB.

¿Cuáles son los beneficios de esta combinación? Se podría utilizar únicamente Raspberry para la elaboración del SAR, pero existen numerosos beneficios que proporciona las placas Arduino frente a la Raspberry y son:

- Menor costo de adquisición del producto en caso de fallos energéticos.
- Mayor flexibilidad y facilidad en la conexión con distintos componentes electrónicos.
- Mayor compatibilidad, con los módulos arduino-compatible y la familia adafruit
- Buen tiempo de respuesta de I/O.
- Alta confiabilidad en la lectura de sensores y en los valores de manipulación de actuadores.

Varios de estos beneficios se deben a que Arduino no posee un sistema operativo, sino un único programa que se ejecuta indefinidamente (LOOP) sin necesidad de correr algún software auxiliar que lo dispare o ejecutando como servicio; logrando concentrar su poder de procesamiento en el único programa definido. La ejecución de servicio genera retrasos propios de sistemas operativos.

### 8.2.4 Cámara V2 de Raspberry Pi

La cámara V2 de Raspberry, es una cámara exclusiva de esta plataforma la cual se conecta al puerto CSI de cualquier modelo de este computador (desde la Raspberry Pi 1 hasta el modelo actual, ósea, la Raspberry Pi 3), lo cual permite obviar la conexión pin a pin y abstraernos de la comunicación y procesamiento de la cámara. Como se comentó en el capítulo 4, es una cámara de alta definición de 8 megapíxeles, suficiente para el objetivo que se pretende con el desarrollo del SAR. Esto soluciono las problemáticas que se nos presentaron a la hora de probar la cámara OV7670 con Arduino; como el poder de procesamiento de imágenes y transmisión de las mismas (inalámbricamente) hacia otro dispositivo tal como una PC o un dispositivo móvil (en nuestro caso smartphones).

### 8.2.5 Módulos de Arduino

Dentro de los módulos, sensores y actuadores de Arduino que se probaron y/o se utilizan, se encuentran:

Utilizados en el sar:

- El módulo GPS, será utilizado para determinar la ubicación geográfica del SAR (Geolocalización)
- Sensor de temperatura KY-001(-55° a +125°)
- Sensor ultrasonido HC-SR04 para determinar presencia de objetos a determinadas distancia y tratar de evitar el impacto con los mismos
- Motores CC para la movilidad del SAR dentro del ambiente

Ensayados y no seleccionados:

- El módulo wifi ESP8266 y el módulo Bluetooth HC-05, no se utilizarán debido a que la Raspberry Pi3 Model B, brinda su funcionalidad.
- El módulo Acelerómetro MMA7361.
- Servomotor sg90.
- Sensor de evasión de obstáculos KY032.
- Sensor de golpe KY-031.
- Sensor de llamas KY-026.

AGREGAR REFERENCIAS A ANEXO DE PRUEBAS

## 8.3 Selección tecnologías software

### La selección del software, necesario para el desarrollo del SAR, se basa en los siguientes requerimientos:

### Generar un mayor nivel de abstracción, mediante librerías basadas en JavaScript, para la comunicación con el hardware.

### Utilizar un Sistema Operativo de base (en nuestro caso Raspbian), en vez de una rutina corriendo en un microcontrolador.

### Tener los recursos necesarios para desplegar un servidor.

### Contar con la posibilidad de comunicar las plataformas Arduino al servidor mediante un protocolo estándar.

### Aprovechar las herramientas de Raspbian para realizar la comunicación y captura de imágenes.

### Necesitar el desarrollo de una aplicación móvil para el control inalámbrico del SAR.

### Almacenar datos para la generación de estadísticas.

### Permitir el acceso a más de un cliente a los datos alojados en él SAR.

### Para cumplir con los requisitos mencionados anteriormente se escogieron las siguientes de tecnologías.

Como se mencionó en un apartado anterior (8.2.1 ¿Por qué Arduino?) en cuanto a las dificultades que surgieron al tratar de utilizar la cámara OV7670 con el Arduino Mega, es que se decidió adquirir la Raspberry Pi 3 modelo B. Esta plataforma cuenta con una cámara (mencionada en el apartado 4.6 Accesorios para Raspberry Pi) como accesorio, la cual permite la captura de imágenes mediante aplicativos compatibles con Debian, como consecuencia también compatible con Raspbian.

Se opto por la instalación de Raspbian en la Raspberry, porque es el sistema operativo oficialmente soportado por la fundación[^1]. La placa Arduino se encuentra pensada para desarrollos donde existe un único proceso de ejecución principal. Esto genera limitaciones en cuanto a memoria, procesamiento y almacenamiento como, por ejemplo:

- Para poder almacenar gran cantidad de datos es necesario contar con un módulo para memorias SD. Este módulo funciona con comunicación serial.
- El almacenamiento disponible no permite el uso de bases de datos.
- Posee una cantidad limitada de interrupciones por hardware (2 en Arduino Uno y Nano, 6 en el caso de Arduino Mega). No cuenta con la posibilidad de interrupciones por software.
- La detección de nuevo valores en sensores se realiza por pooling. Esto significa, consultar el estado de cada uno de los sensores.
- No es suficiente el tiempo de transmisión de imágenes dado el nivel de procesamiento para almacenar bytes en un buffer y retransmitirlos. Este fue el caso de la captura de valores de la cámara y su retransmisión via serie (cable). Además, de no alcanzar los FPS (frame per seconds) necesarios para una visualización fluida (al menos 10 FPS) ver anexo, se nos dificultó lograr el objetivo de la transmisión de las imágenes por medios inalámbricos (Bluetooth y Wifi).

Por otro lado, la Raspberry al ser un computador que permite la instalación de un sistema operativo, facilitó resolver varias de las dificultades, antes mencionadas, que sucedieron con los microcontroladores.

En los repositorios de Raspbian encontramos una aplicación denominada Motion. La cual surgió para satisfacer la videovigilancia a través de cámaras web. En nuestro caso, nos permitió la captura de imágenes con la cámara de Raspberry abstrayéndonos de la comunicación entre la aplicación y el hardware.

Dadas las capacidades inalámbricas que posee la Raspberry es que se pudo configurar la misma en modo Access Point (AP, o punto de acceso en español Glosario). Esto quiere decir, crear una red inalámbrica wifi (con una ssid y contraseña) sin depender de ningún dispositivo de red externo (como por ejemplo un router inalámbrico) y permitiendo la conexión de diversos hosts (Glosario), donde cada uno obtiene su respectiva ip por medio de dhcp.

Al comenzar el desarrollo de esta tesina, y teniendo en cuenta que íbamos a trabajar únicamente con la familia Arduino, decidimos diseñar una aplicación móvil nativa. Dado que la única comunicación que existía entre un posible cliente y el SAR era por datos raw (Glosario) enviados por bluetooth o wifi.

Para diseñar esta app se investigaron distintas herramientas (explicadas en el Capítulo 5 - Aplicaciones Móviles), sin embargo, al cambiar las prestaciones hardware y tener un sistema operativo, se decidió cambiar la arquitectura del software del SAR.

Esta nueva arquitectura genero un cambio en la aplicación, o sea, se pasó del desarrollo de una app nativa, para Android, a una app web. Esto permitió crear una única aplicación que puede ser consumida por distintos dispositivos que accedan a la red LAN (Glosario) del SAR.

Para producir la app web se necesitó de un grupo de tecnologías que satisfagan los siguientes puntos:

- Contar con la posibilidad de almacenar datos de los sensores y acciones realizadas mediante una base de datos.
- Tener una interfaz de fácil comunicación con el servidor.
- Tener la capacidad de desplegar a demanda la app desde una red LAN.
- Diseñar una app, utilizando herramientas de frontend, para el renderizado en el cliente.
- Permitir que esta app utilice las acciones http para la comunicación con el servidor.

Teniendo en cuenta los puntos anteriores examinamos distintas herramientas de desarrollo de aplicaciones web móviles (como se vieron en el Capítulo 5 - Aplicaciones Móviles). Estas tecnologías son: Cordova, IntelXDK, Meteor y MEAN.

Tanto Cordova como IntelXDK fueron descartadas dado que se prefirió un grupo de herramientas, compatibles entre ella, y estables (stack de desarrollo de software).

Por otro lado, se trató de incursionar en Meteor, realizando aplicaciones sobre arquitecturas Intel x86/x64. Se diseño un prototipo funcional de la aplicación, pero al migrar la misma a la arquitectura ARM (en nuestro caso la de Raspberry Pi) tuvimos inconvenientes dado que este framework no se encontraba soportado oficialmente para esta arquitectura. Existía un fork, pero no tuvimos éxito en la integración de las tecnologías, que integran Meteor, a pesar de lograr compilarlo.

Meteor se encuentra conformado por el siguiente conjunto de herramientas: Mongo, Blaze, Meteor, Iron (explicadas en referencia capítulo 5 ). Al presentarse la dificultad, antes mencionada, es que seleccionamos el stack MEAN el cual resultó ser compatible con el desarrollo avanzado hasta el momento, hecho con Meteor.

El stack MEAN (visto Capítulo 6 – Stack MEAN) compuesto por Mongo, Express, Angular y Node. La migración de la aplicación tanto frontend como backend, desarrollada con Meteor, fue dispuesta de la siguiente forma: El procesamiento de templates, captura y gestión de eventos, realizada en Blaze, se trasladó a Angular 4+. El servidor Meteor se codificó en Node. El manejo de rutas y REST desarrollado en Iron se migró a Express. En cuanto a las colecciones de datos se mantuvieron en Mongo.

Otro desafío que se presentó, era comunicar el servidor (realizado con Node) corriendo en Raspbian (dentro de la Raspberry) con las placas Arduino Mega y Arduino Nano. Avanzando sobre NPM, se encontraron dos librerías estables para la comunicación de Node y Arduino. Estas librerías son Cylon[^2] y Johnny-five. La librería Cylon utiliza el paradigma de programación declarativo, en cambio, Johnny-five el funcional. Este último fue el seleccionado por mantener el mismo estilo de codificación que el stack MEAN, compatibilidad con los componentes de Arduino y poseer una versión estable de serialport compatible con la arquitectura ARM.

Para poder realizar la comunicación entre Node y las placas Arduino, Johnny-five se vale de un protocolo de comunicación estándar (Capítulo 7 – Librería Johnny-five y el protocolo Firmata) denominado Firmata.

Finalmente, se definió una secuencia de eventos, que permiten capturar los valores sensados para poder insertarlos en las colecciones de Mongo. Con estas colecciones se generan las estadísticas requeridas por los objetivos de esta tesina.

## Resumen

En este capítulo se analizaron las diversas tecnologías tanto de hardware como de software utilizadas en el SAR, justificando la selección de cada una de ellas y los ensayos realizados para concluir en su utilización.

Se explicó el porqué del uso de Arduino y Raspberry Pi como plataformas de base para la manipulación del robot móvil. Las ventajas del uso de la cámara v2 de Raspberry, y las problemáticas que se presentaron al probar la cámara para Arduino OV7670.

Por otro lado, en cuanto al software seleccionado, se detallaron los requerimientos lógicos necesarios para el desarrollo del SAR. Dentro de los mismos, se destaca la posibilidad de contar con un Sistema Operativo, el cual finalmente fue Raspbian. Luego se describen las diversas tecnologías de desarrollo que se probaron, resultando ser el satck MEAN el elegido para realizar la aplicación web.

[^1] https://www.raspberrypi.org/downloads/raspbian/
[^2]

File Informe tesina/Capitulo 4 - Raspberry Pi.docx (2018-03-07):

# Capítulo 4 – Raspberry Pi

En este capítulo se va a analizar y detallar el SBC Raspberry Pi, el cual tomó un papel fundamental en el desarrollo del SAR, siendo el mismo el centro de mando del robot móvil. Se detallan las especificaciones técnicas de las principales versiones de esta plataforma, donde se puede apreciar la evolución, en cuanto al hardware, que ha ido teniendo.

Por otro lado, se introduce el concepto de GPIO, que no son más que pines de Entrada/Salida de propósito general, para la conexión de diversos sensores, módulos y/o actuadores que se deseen comunicar, en este caso, con la Raspberry Pi.

Además, se presentan variados sistemas operativos y accesorios complementarios compatibles con Raspberry Pi. Dentro de los accesorios se describe la cámara V2 de esta plataforma utilizada en el SAR.

Para finalizar el capítulo se describen una serie de ventajas que presenta esta plataforma con respecto a otras similares.

## 4.1 Raspberry Pi

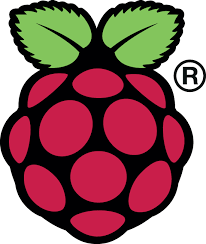
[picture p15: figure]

Raspberry Pi es un computador de placa reducida (SBC) desarrollado en Reino Unido por la Fundación Raspberry Pi. Su lanzamiento fue el 29 de febrero del 2012 con el Raspberry Pi 1 Modelo A. Su costo es relativamente bajo en relación a sus especificaciones técnicas (alrededor de U$D 25), dado que su objetivo primordial es el de estimular la enseñanza de la informática en las escuelas. Su logo oficial, como se muestra en la imagen (Ilustración 20 - Logo oficial de Raspberry Pi), no es más que una frambuesa.

Ilustración 20 - Logo oficial de Raspberry Pi
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

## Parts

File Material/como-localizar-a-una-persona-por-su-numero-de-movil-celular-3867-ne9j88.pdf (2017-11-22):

# Cómo localizar a una persona por su número de móvil (celular)

Octubre 2014

Localizar a una persona por su celular es posible, sobre todo gracias a las tecnologías que permiten localizar un teléfono móvil en caso de robo o simplemente si no sabes dónde lo has dejado.

Cómo rastrear un teléfono Android
(Samsung)
Cómo localizar un iPhone
Cómo ubicar un teléfono BlackBerry Localizar teléfonos con Symbiam

Para que esto funcione efectivamente, el teléfono móvil deberá contar con una aplicación instalada

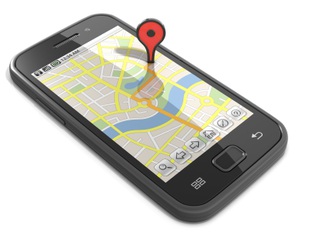
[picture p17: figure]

previamente. En algunos casos basta simplemente
configurarlo. También es importante que el teléfono
móvil o celular esté encendido al momento de efectuar el rastreo. Por lo tanto, si el móvil no tiene batería o está apagado, no será posible rastrearlo. Algunas aplicaciones y/o páginas te permiten también localizarlo en un mapa desde Internet.

## Cómo rastrear un teléfono Android (Samsung)

Consulta la ficha: Localizar un teléfono Android desde una página web (http://es.kioskea.net/faq/6724-android-lost-localiza-tu-telefono-android-desde-una-pagina-web) o ingresa directamente al Administrador de dispositivos Android (http://es.kioskea.net/faq/6724-localiza-tu-dispositivo-movill-android-desde-una-pagina-web) si tienes una cuenta Gmail.

## Cómo localizar un iPhone

Consulta la ficha: Localizar tu iPhone en caso de robo o pérdida. (http://es.kioskea.net/faq/8107-localiza-tu-iphone-en-caso-de-robo-o-perdida)

## Cómo ubicar un teléfono BlackBerry

Para poder localizar un BlackBerry, deberás instalar BlackBerry Protect. (http://es.blackberry.com/services/protect/)

## Localizar teléfonos con Symbiam

Instala la aplicación DondeEsta (http://es.kioskea.net/download/descargar-9339-dondeesta-para-symbian) (para Symbiam), con ella podrás localizar tu móvil en caso de robo o pérdida por descuido. Te permite también saber dónde están tus hijos. El procedimiento es fácil: descarga DondeEsta (http://es.kioskea.net/download/descargar-9339-dondeesta-para-symbian) e instálalo en tu smartphone o en el equipo que quieras monitorear. Ejecútalo y ve a las opciones del menú. Autoriza a los contactos que te podrán ubicar (o si tienes una segunda línea, autorízate a ti mismo para poder ubicar tu móvil en caso de que lo pierdas). Importante: este procedimiento no funciona con los contactos de la tarjeta SIM, sino con los del propio teléfono. Por ello, deberás pasarlos previamente. Para ubicar el teléfono que quieres localizar, debes mandar un simple SMS con tres signos de interrogación (???) desde cualquier móvil autorizado y que no necesite tener el programa instalado. Recibirás como respuesta un SMS con la ubicación aproximada y con un enlace a un mapa, que podrás abrir en tu navegador, para tener una mejor visualización de la posición geográfica de tu móvil. Obtendrás una mayor precisión sobre la ubicación de tu móvil si este cuenta con GPS. El costo de los SMS varía en función de tu plan de datos.

Este documento intitulado « Cómo localizar a una persona por su número de móvil (celular) (http://es.kioskea.net/faq/3867-como-localizar-a-una-persona-por-su-numero-de-movil-celular) » de Kioskea (http://es.kioskea.net) (es.kioskea.net) esta puesto a diposición bajo la licencia Creative Commons. Puede copiar, modificar bajo las condiciones puestas por la licencia, siempre que esta nota sea visible.

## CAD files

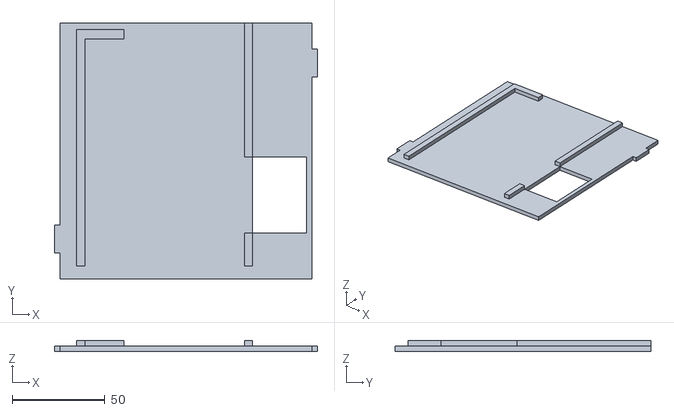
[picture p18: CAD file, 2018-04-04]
Modelo 3d/cuartoPisoFinalV2.stl
142.0 x 138.0 x 6.00

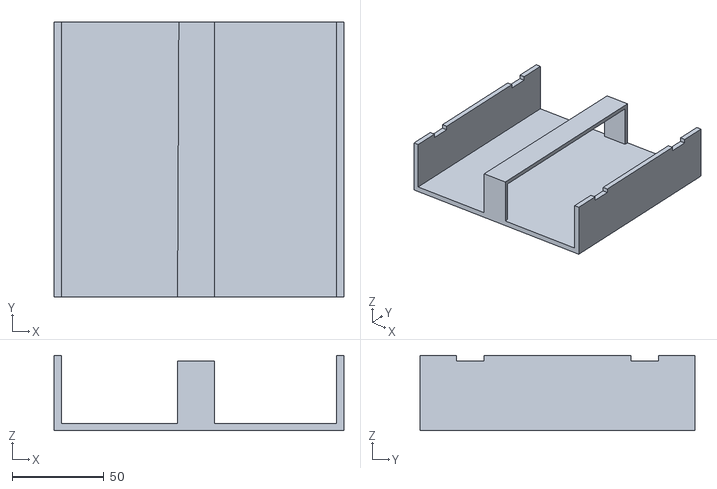
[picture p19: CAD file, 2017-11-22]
Modelo 3d/Tesis-base sola.stl
158.0 x 150.0 x 41.0

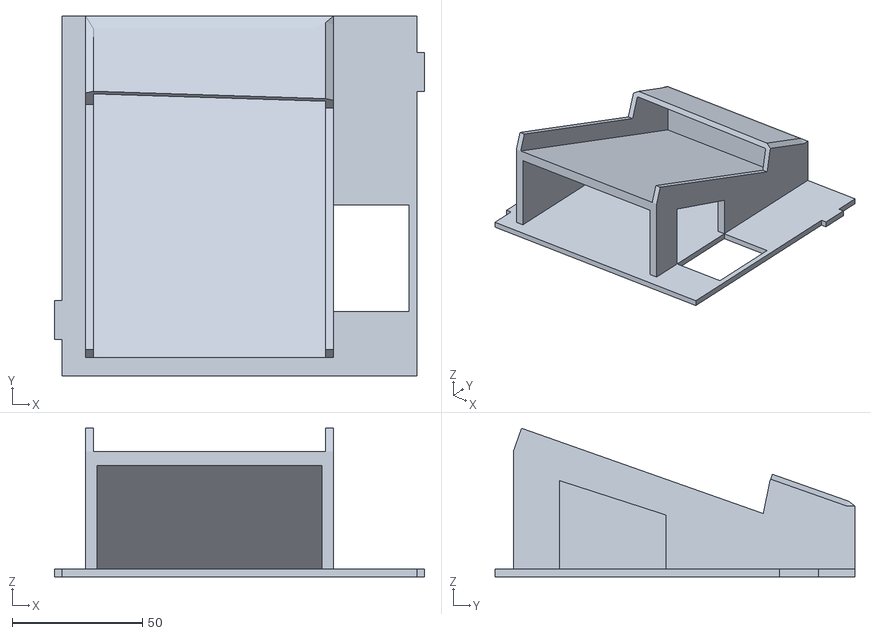
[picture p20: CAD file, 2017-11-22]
Modelo 3d/cuartoPisoV2.stl
142.0 x 138.0 x 56.9

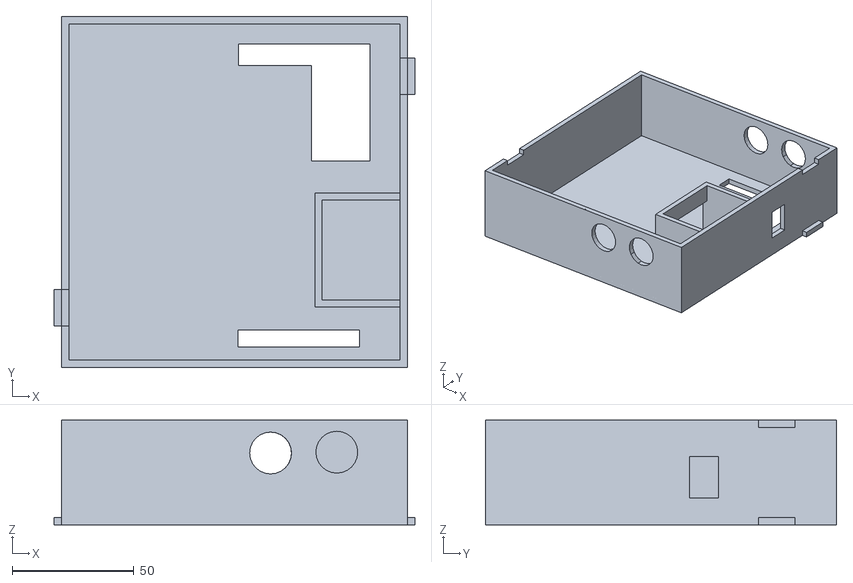
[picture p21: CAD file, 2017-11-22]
Modelo 3d/tercerPiso.stl
148.0 x 144.0 x 43.0

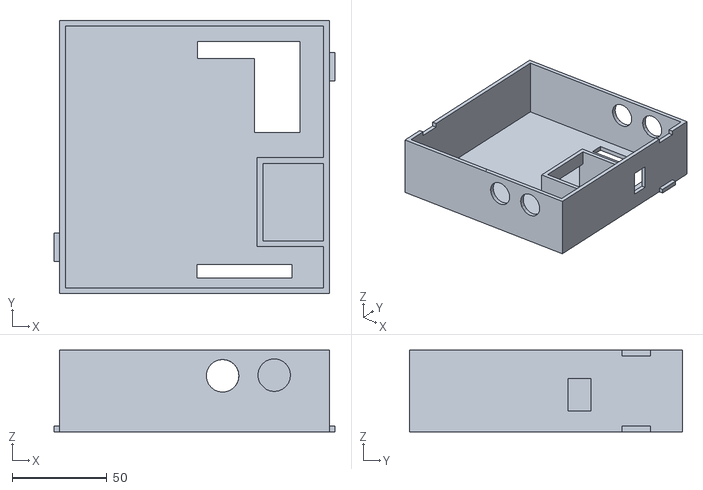
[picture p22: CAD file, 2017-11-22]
Modelo 3d/tercerPisoSlicer.stl
148.0 x 144.0 x 43.0

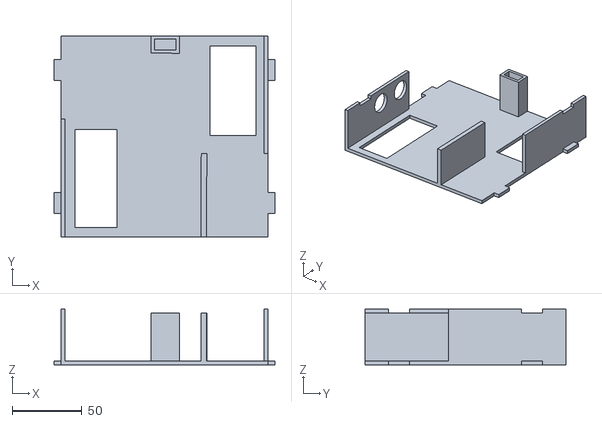
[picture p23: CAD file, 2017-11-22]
Modelo 3d/segundoPiso.stl
158.0 x 144.0 x 40.0

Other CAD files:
Modelo 3d/cuartoPisoFinal.stl
Modelo 3d/cuartoPiso.stl
Modelo 3d/Rueda.skp
Modelo 3d/cuartoPiso.skp
Modelo 3d/cuartoPisoFinal.skp
Modelo 3d/segundoPiso.skp
Modelo 3d/tercerPiso.skp

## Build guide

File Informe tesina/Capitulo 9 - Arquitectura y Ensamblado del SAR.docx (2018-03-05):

# Capítulo 9 – Arquitectura y Ensamblado del SAR

Para el desarrollo de esta tesina se procedió a armar un prototipo del SAR mediante un robot móvil, el cual cuenta con una variedad de actuadores y sensores que le permiten interactuar con el entorno que lo rodea. En este capítulo, se describen los diversos componentes del SAR, con sus respectivas funciones dentro del mismo, así como también, los procedimientos que se llevaron a cabo para construirlo. Se muestran los distintos niveles en los cuales se estructura y como se disponen los elementos dentro de él. En la siguiente imagen (Ilustración 47 - Esquema de conexión de componentes) se puede apreciar la arquitectura de conexión de los componentes que integran al SAR.

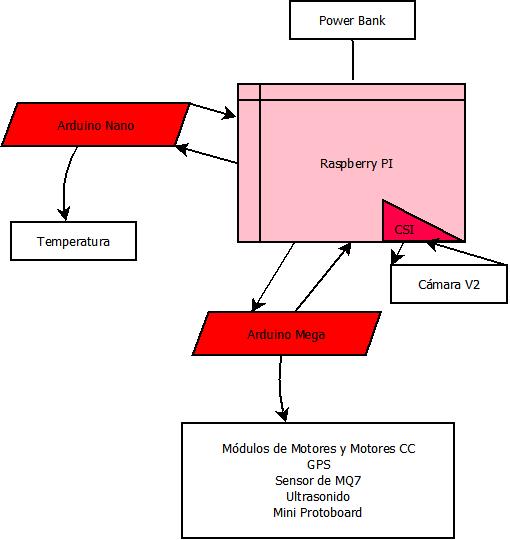
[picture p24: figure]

Ilustración 47 - Esquema de conexión de componentes

## 9.1 Componentes

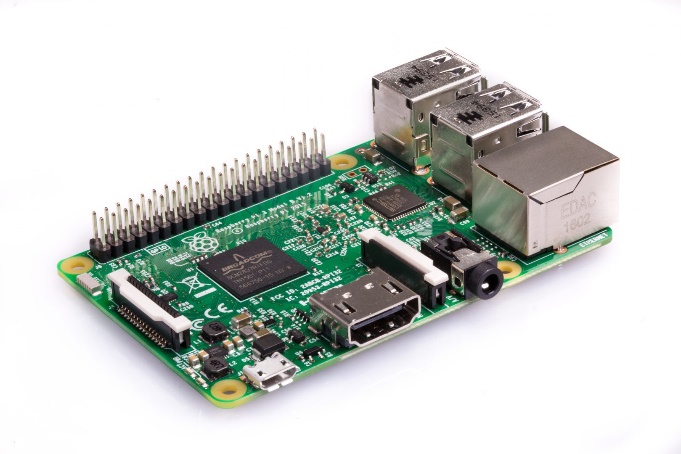
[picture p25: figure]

Una Raspberry Pi 3 model B: Componente principal del SAR, es el servidor del mismo, encargado de almacenar la aplicación web y recibir las peticiones de los clientes para luego mandar las ordenes a las placas Arduino. Cuenta con una tarje microSD donde almacena el sistema operativo Raspbian el cual se ejecuta al encenderla y permite correr la aplicación desarrollada.

Ilustración 48 - Raspberry Pi 3

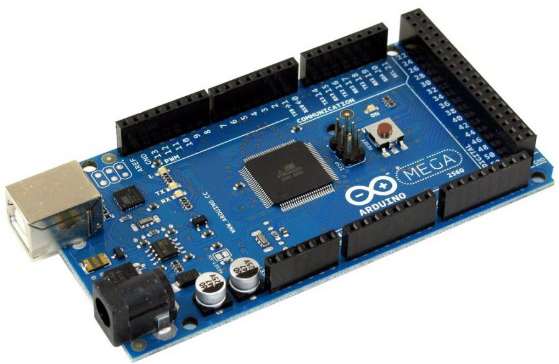
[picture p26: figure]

Un Arduino Mega: Es el principal controlador del SAR, en él se conectan todos los sensores y actuadores (a excepción del sensor de temperatura). Funciona como intermediario entre la Raspberry y el resto de los componentes, dado que recibe todas las ordenes de ejecución de la misma. En su memoria, se encuentra almacenada una versión del protocolo Firmata nombrada como StandarFirmata (dado por la librería Firmata de Arduino, Anexo X) necesaria para establecer la comunicación con los comandos enviados desde Javascript por la aplicación web.

Ilustración 49 - Arduino Mega

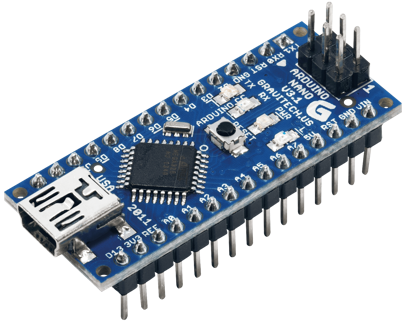
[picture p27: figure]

Un Arduino Nano: Esta versión de Arduino es la que se encarga de capturar la temperatura obtenida por el sensor DS18B20. Se debió optar por el uso de otro Arduino, dado que para la captura de temperaturas y el envío de los datos a la Raspberry mediante JavaScript se necesita una versión particular del protocolo Firmata, nombrada como ConfigurableFirmata (Anexo X1).

Ilustración 50 - Arduino Nano

Cuatro motores DC (corriente continua de 3v a 6v) con caja reductora: Estos motores, en conjunto con cuatro ruedas de plástico cubiertas con una goma cada una, son los que permiten darle la movilidad al SAR.

Ilustración 51 - Motores CC

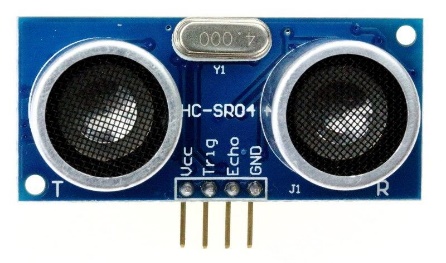
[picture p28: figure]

Tres sensores ultrasónicos HC-SR04: Los sensores ultrasónicos, se utilizan para determinar la presencia de algún objeto a una distancia menor a 20 centímetros, tanto al frente del SAR como en sus laterales. Al identificar un objeto a una distancia menor a la mencionada, se bloquea el avance del robot en la dirección en donde se encuentre dicho objeto.

Ilustración 52 - Sensor de ultrasonido

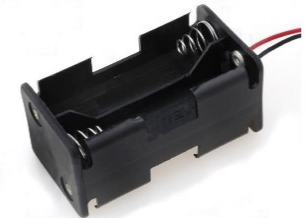
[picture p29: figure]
Resultado de imagen para portapilas aa x 4

Dos portas pilas AA x4 con sus respectivas pilas recargables: Utilizados para alimentar de corriente eléctrica a los 4 motores.

Ilustración 53 - Porta pilas

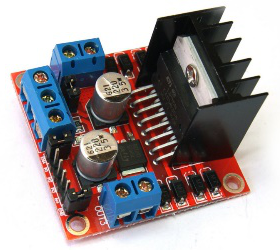
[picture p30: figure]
Resultado de imagen para puente h l298n

Dos puentes H L298N: Son los intermediarios entre el Arduino Mega y los motores, cada uno de ellos se encarga de la manipulación de dos motores.

Ilustración 54 - Módulo Puente H

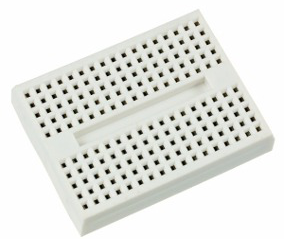
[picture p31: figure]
Resultado de imagen para mini protoboard

Una mini Protoboard: Utilizada como extensión de pines, más que nada para los pines GND y 5v de la placa Arduino Mega.

Ilustración 55 - Mini-protoboard

Un sensor de temperatura DS18B20 montado sobre una placa KY-001: Este módulo es el encargado de sensar la temperatura, se encuentra conectado al Arduino Nano.

Ilustración 56 - Sensor de Temperatura

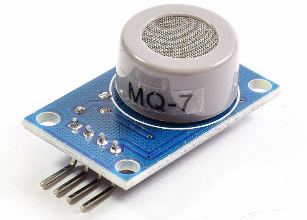
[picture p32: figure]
Resultado de imagen para sensor de monoxido mq7

Un sensor de monóxido de carbono MQ-7: El sensor de monóxido, conectado al Arduino Mega, detecta la ausencia o presencia de dicho gas.

Ilustración 57 - MQ7 CO

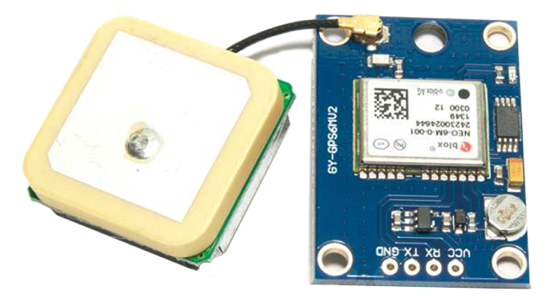
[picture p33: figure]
Imagen relacionada

Un GPS GY-GPS6MV2: Con este módulo de GPS obtenemos toda la información necesaria con respecto a la Geolocalización del SAR (latitud, longitud, punto cardinal, velocidad, orientación, fecha y hora).

Ilustración 58 - GPS

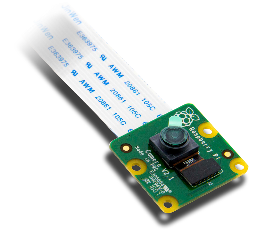
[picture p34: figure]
Resultado de imagen para Cámara Raspberry Pi V2

Ilustración 59 - Cámara V2

Cámara de Raspberry Pi V2: Esta cámara, exclusiva de Raspberry, es la utilizada para captar con señal de video en tiempo real (mediante el software motion) el entorno que rodea al SAR.

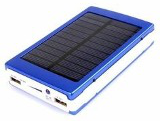
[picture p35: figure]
Resultado de imagen para power bank solar malibu

PowerBank Malibu de 20Ah con panel solar: Funciona como batería del SAR, provee de corriente eléctrica a la Raspberry y por ende a los arduinos conectados a ella.

Ilustración 60 - Panel Solar Power Bank

## 9.2 Estructura

### 9.2.1 Diseño

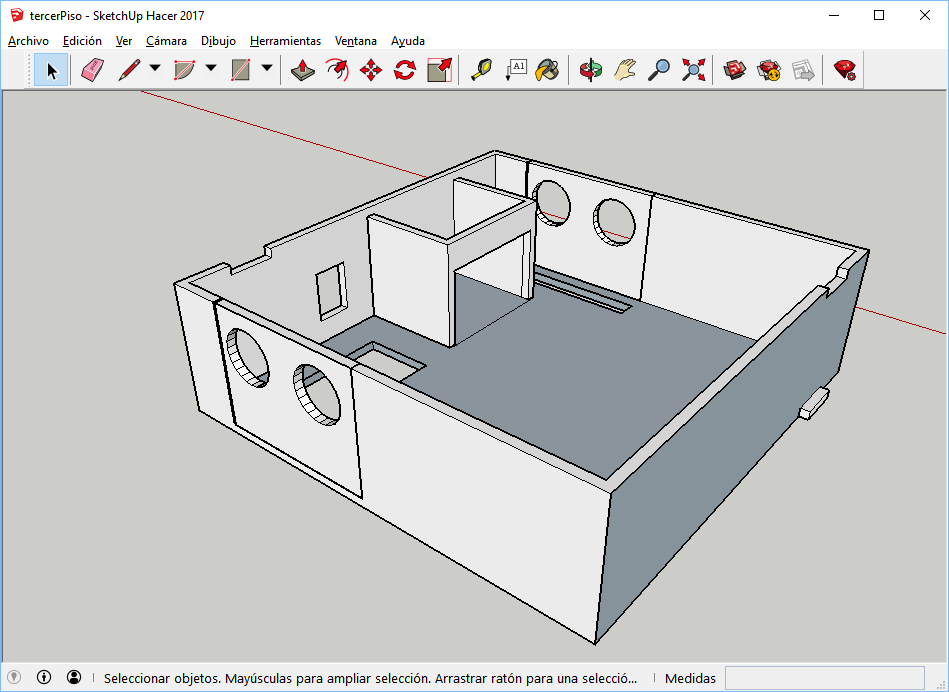
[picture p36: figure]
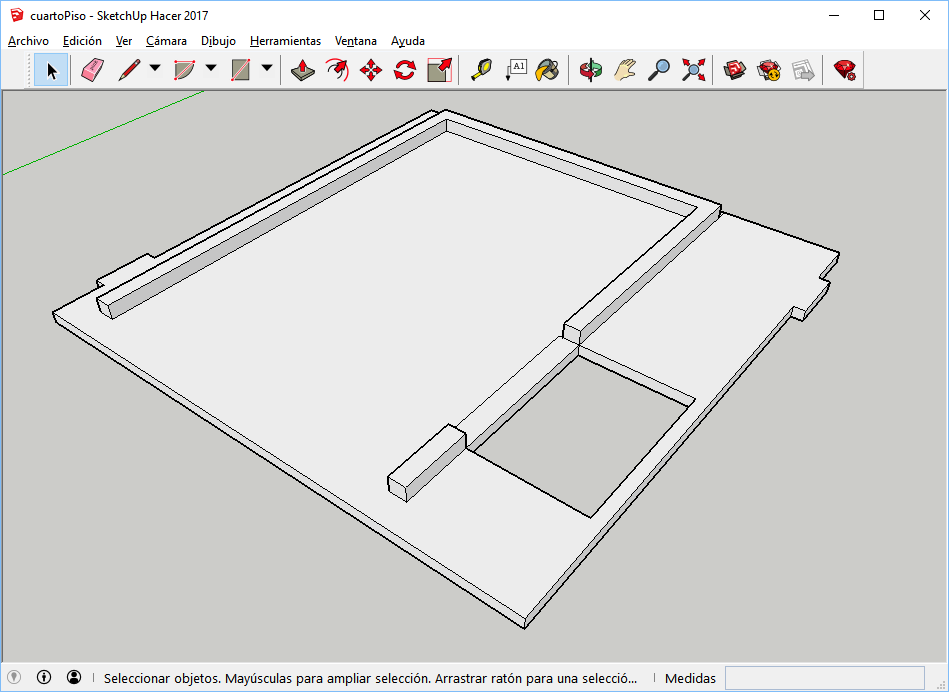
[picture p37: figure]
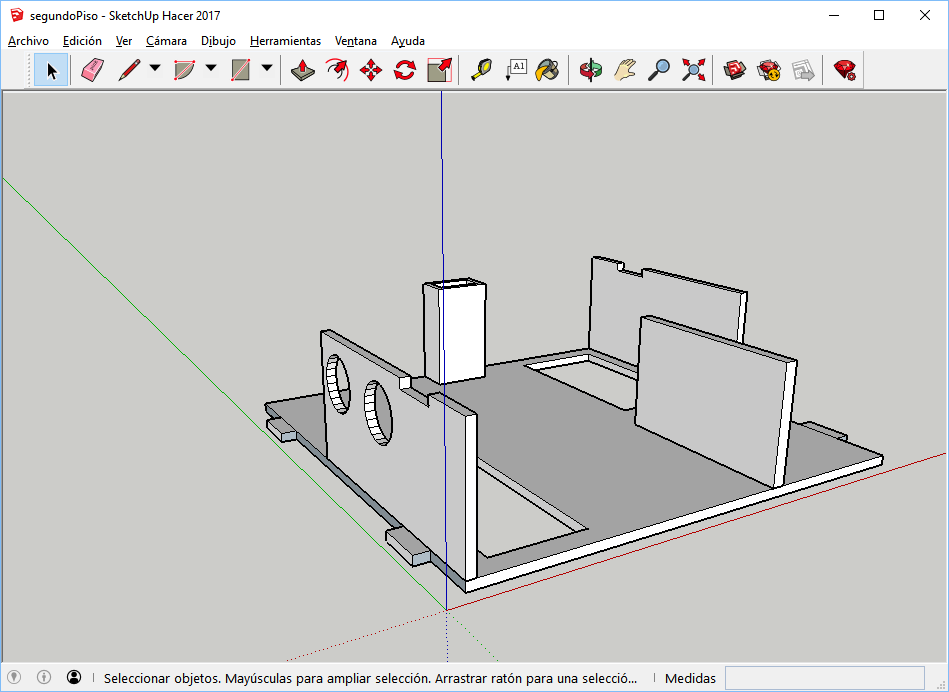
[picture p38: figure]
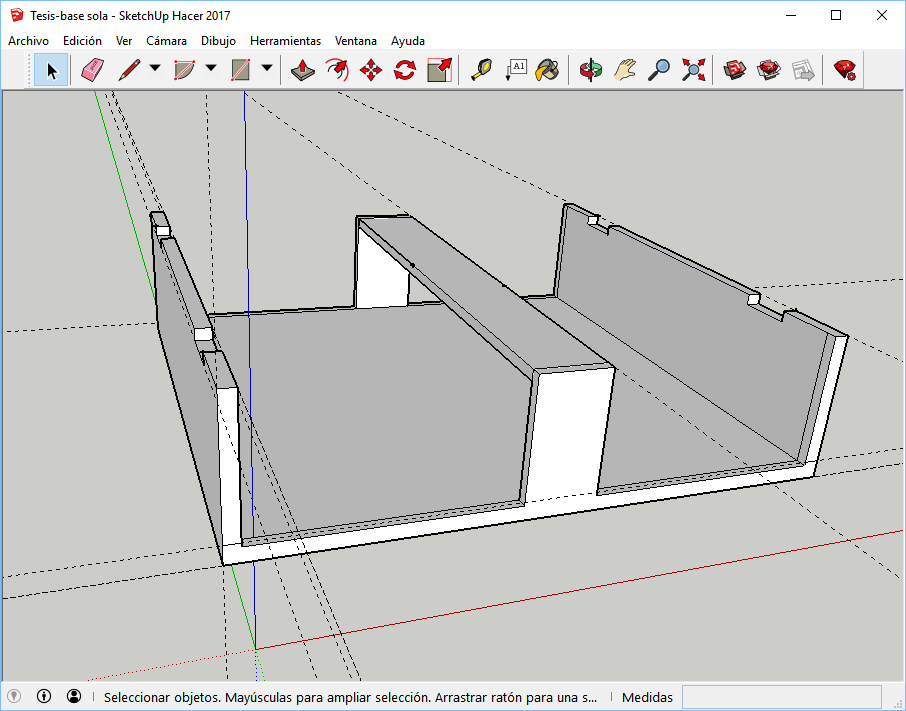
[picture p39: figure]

Para el armado de la estructura se procedió a diseñar en 3D las distintas piezas por medio del entorno de diseño gráfico SketchUp 2017. Se tomaron medidas de los distintos componentes y en base a ellas decidimos dividir el gabinete del SAR en cuatro niveles.

Ilustración 61 - Diseño estructura nivel 3 con SketchUp

Ilustración 62 - Diseño estructura nivel 4 con SketchUp

Ilustración 63 - Diseño estructura nivel 1 con SketchUp

Ilustración 64 - Diseño estructura nivel 2 con SketchUp

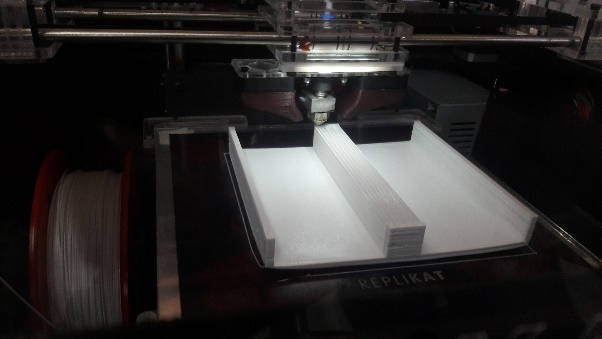
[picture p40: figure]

Una vez armados los modelos de los distintos niveles, fuimos imprimiendo los mismos mediante una impresora 3D.

Ilustración 65 - Impresión 3D del nivel 1

### 9.2.2 Los 4 niveles

Nivel 1: El primer nivel es en donde se instalaron los motores, con distintas piezas estructurales metálicas diseñadas exclusivamente para dicha función, además se encuentran los dos puentes H L298N conectados a cada par de motores respectivamente. Cada motor cuenta con su rueda de plástico.

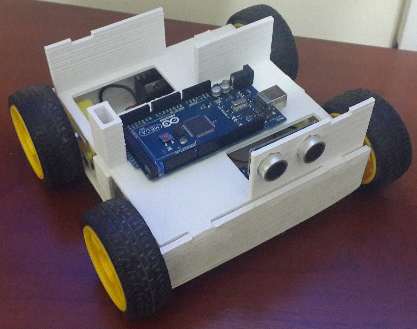
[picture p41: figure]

Nivel 2: En este nivel se adhirió con tornillos el Arduino Mega y la mini protoboard cada uno con sus respectivas conexiones, además del porta pilas utilizados para la alimentación de los motores. En su frente se colocó uno de los sensores ultrasónicos HC-SR04 que verifica la presencia de objetos en la parte delantera del SAR.

Ilustración 66 - Nivel 2 descubierto

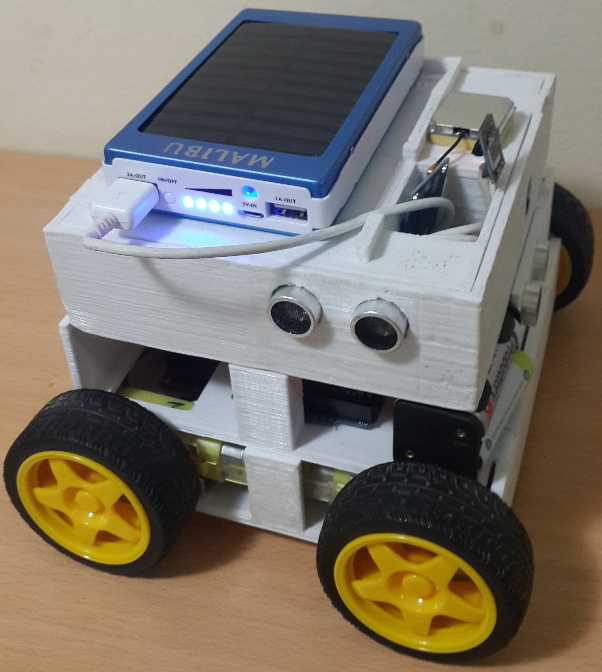
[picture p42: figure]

Nivel 3: En el tercer nivel se encuentra la Raspberry Pi y el Arduino Nano, en conjunto con variados sensores: 2 sensores HC-SR04, ubicados uno en cada lateral para verificar objetos en dichos lugres, 1 sensor de monóxido de carbono MQ-7 y la cámara de Raspberry en el frente.

Ilustración 67 - RM Vista Lateral

Nivel 4: El nivel superior es el que se equipa con la batería portátil solar y que se conecta directamente a la Raspberry, además se encuentra a la vista el GPS y el sensor de temperatura DS18B20. Este último conectado al Arduino Nano.

## 9.3 Esquemas de conexión de componentes Arduino

En las siguientes imágenes se pueden apreciar los esquemas básicos de conexión, a la plataforma Arduino, de los diversos actuadores, sensores y módulos que componen al SAR (antes descriptos).

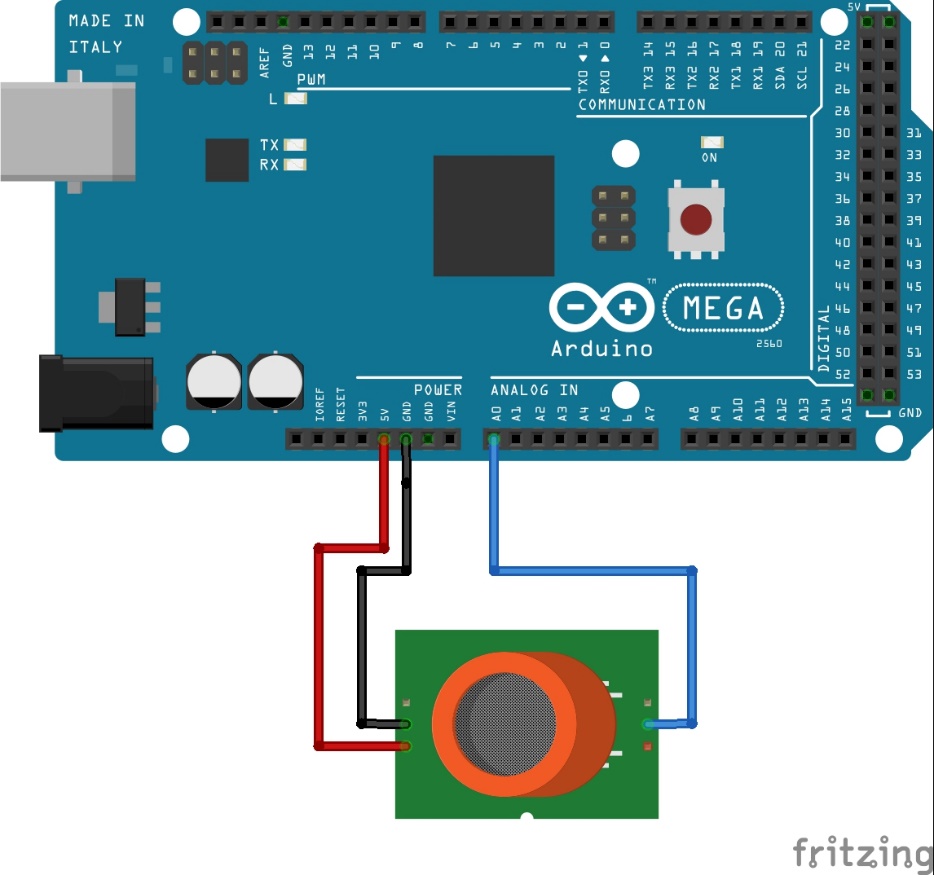
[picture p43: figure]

Ilustración 68 - Esquema de conexión de sensor de monoxido MQ-7 a Arduino Mega

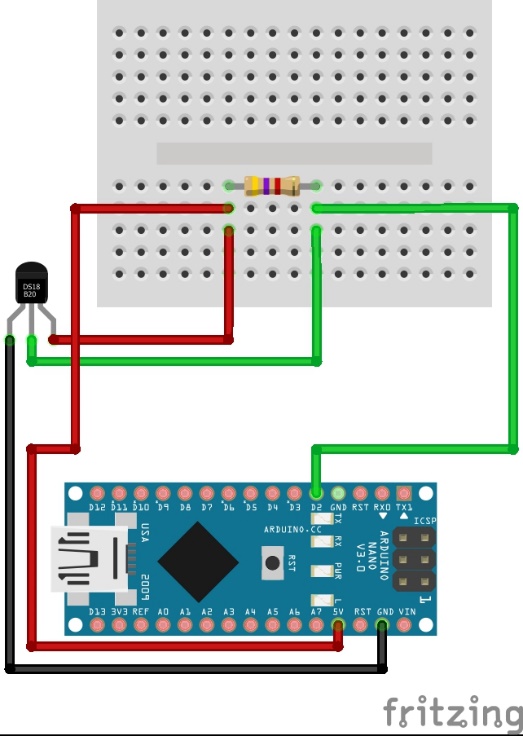
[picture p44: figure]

Ilustración 69 - Esquema de conexión de sensor de temperatura DS18D20 a Arduino Nano

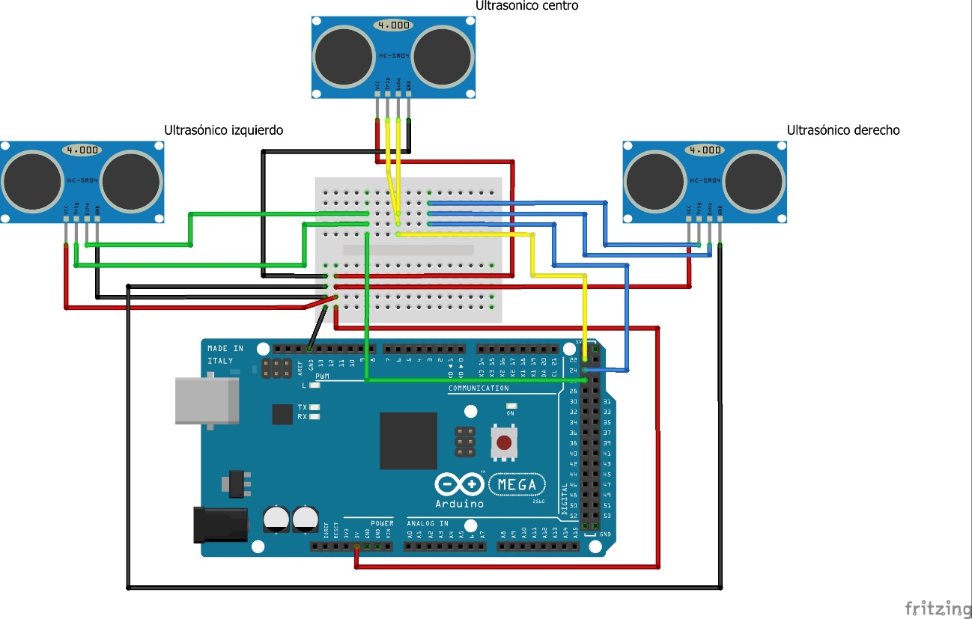
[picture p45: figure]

Ilustración 70 - Esquema de conexión de sensores ultrasónicos HC-SR04 con Arduino Mega

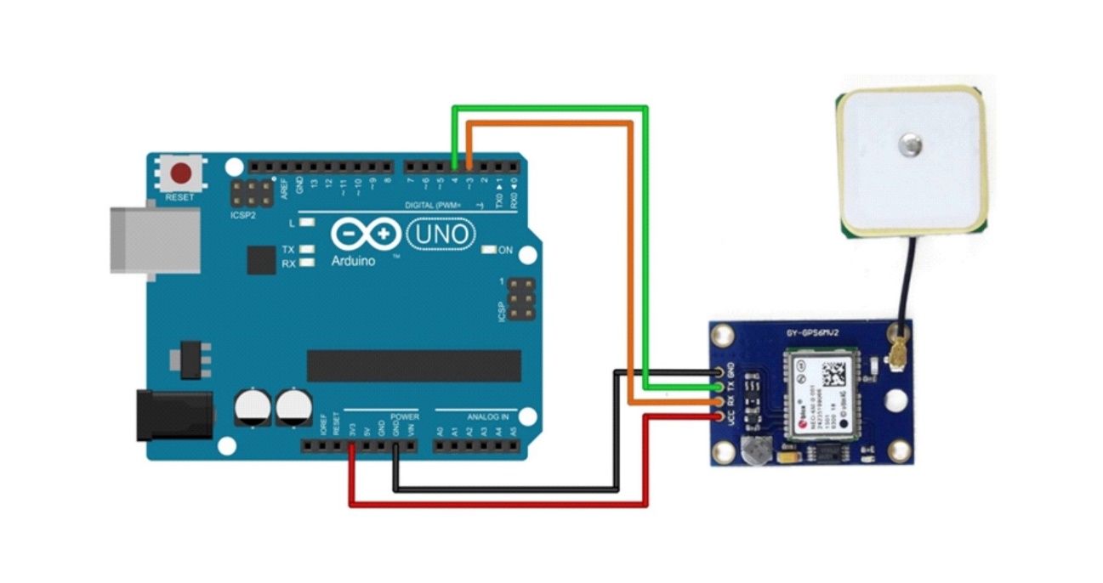
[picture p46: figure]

Ilustración 71 - Esquema de conexión de módulo GPS con Arduino UNO

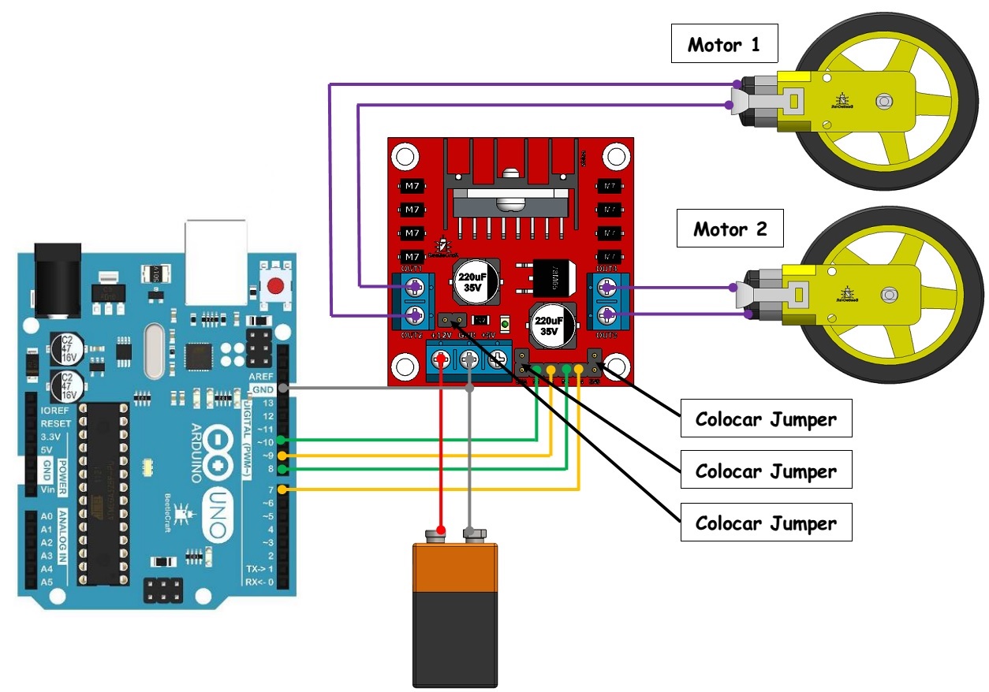
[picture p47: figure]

Ilustración 72 - Esquema de conexión de puente H y motores con Arduino UNO

## Resumen

En este capítulo se pudo apreciar la arquitectura del SAR, para ello se describieron los distintos componentes con los que cuenta. La Raspberry Pi cumple un rol fundamental dentro del robot, dado que es el centro de control del mismo. Contiene la App que permite la manipulación del SAR.

Por otro lado, se vio que, tanto el Arduino Mega como el Nano sirven de intermediarios entre la Raspberry y el resto de los componentes (sensores, módulos y actuadores). Para ello se les debió cargar un protocolo denominado Firmata. Además, se detallaron los esquemas de conexión básicos entre un Arduino y los demás elementos del SAR.

Finalmente, se describió la estructura física del robot y los cuatro niveles con los que cuenta, además de que componentes contiene cada uno.

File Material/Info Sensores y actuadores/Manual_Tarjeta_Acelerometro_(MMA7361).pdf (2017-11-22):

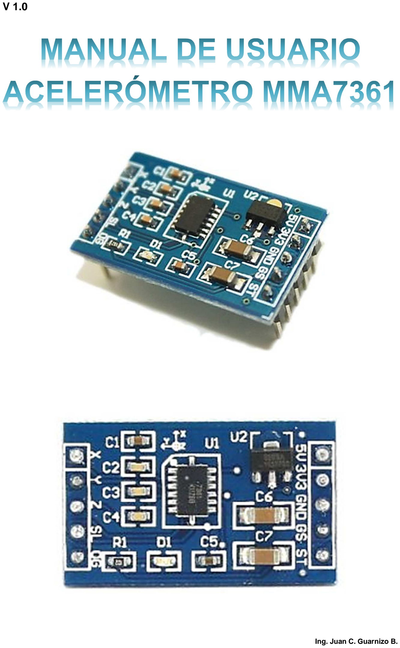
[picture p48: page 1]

V 1.0

Ing. Juan C. Guarnizo B.

2

3

### INTRODUCCIÓN

Los acelerómetros son dispositivos que miden la aceleración, que es la tasa de cambio de la velocidad de un objeto. Esto se mide en metros por segundo al cuadrado (m/s²) o en las fuerzas G (g). La sola fuerza de la gravedad para nosotros aquí en el planeta Tierra es equivalente a 9,8 m/s², pero esto varía ligeramente con la altitud (y será un valor diferente en diferentes planetas, debido a las variaciones de la atracción gravitatoria). Los acelerómetros son útiles para detectar las vibraciones en los sistemas o para aplicaciones de orientación.

¿Cómo funciona un acelerómetro?
Los acelerómetros pueden medir la aceleración en uno, dos o tres ejes. Los de tres ejes son más comunes conforme los costos de producción de los mismos baja.

Generalmente, los acelerómetros contienen placas capacitivas internamente. Algunos de estos son fijos, mientras que otros están unidos a resortes minúsculos que se mueven internamente conforme las fuerzas de aceleración actúan sobre el sensor. Como estas placas se mueven en relación el uno al otro, la capacitancia entre ellos cambia. A partir de estos cambios en la capacitancia, la aceleración se puede determinar.

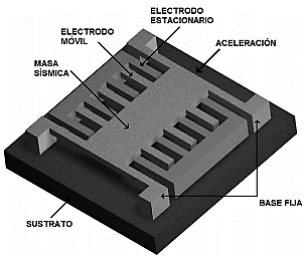
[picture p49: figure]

Figura 1: Sistema micro-electromecánico para la aceleración en 1 eje. Otros acelerómetros se pueden centrar en torno materiales piezoeléctricos. Esta pequeña carga eléctrica de salida estructuras cristalinas cuando se coloca bajo tensión mecánica (por ejemplo aceleración).

4

El sensor MMA7361 es de energía baja, con acondicionamiento de señal, un filtro de paso bajo de 1 polo, compensación de temperatura, prueba automática (Self test), Detecta gravedad 0- caída libre (0g-Detect), y g-Select que permite la selección entre 2 sensibilidades. Desplazamiento de gravedad cero y la sensibilidad se ajustan en fábrica y no requieren dispositivos externos, además incluye un modo de reposo (sleep) que lo hace ideal para dispositivos electrónicos portátiles alimentados por baterías.

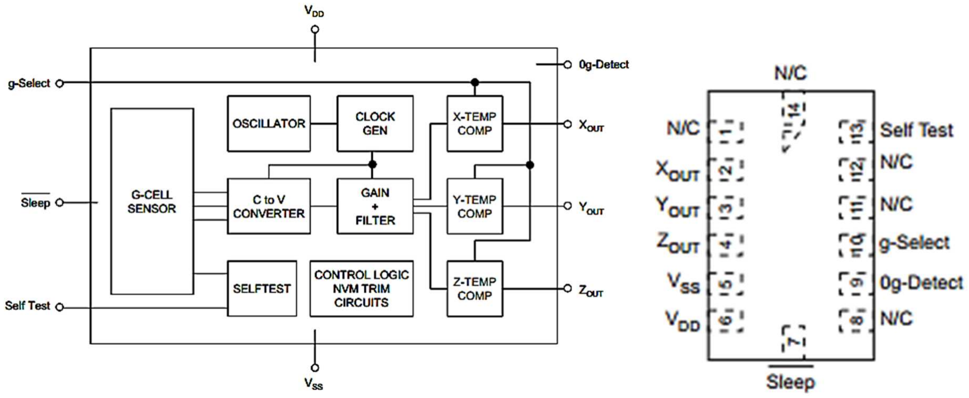
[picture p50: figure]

Figura 2: Diagrama MMA7361 Debemos tener en cuenta que las aceleraciones dinámica (Figura 3), y estática (Figura 4).

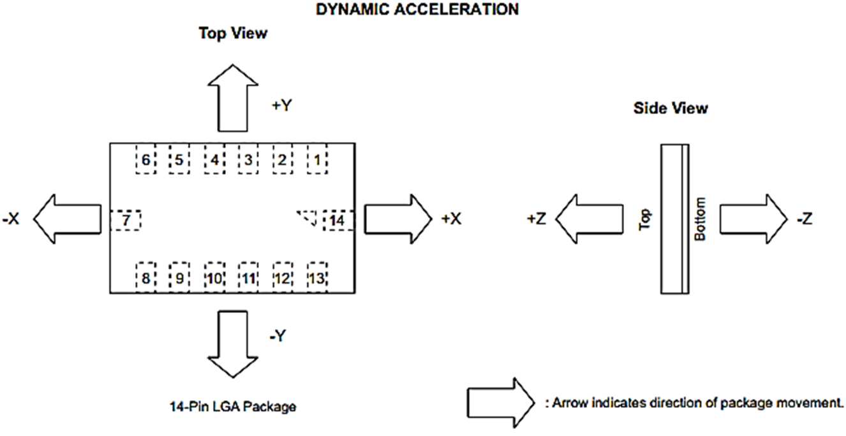
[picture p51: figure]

Figura 3: Aceleración Dinámica.

5

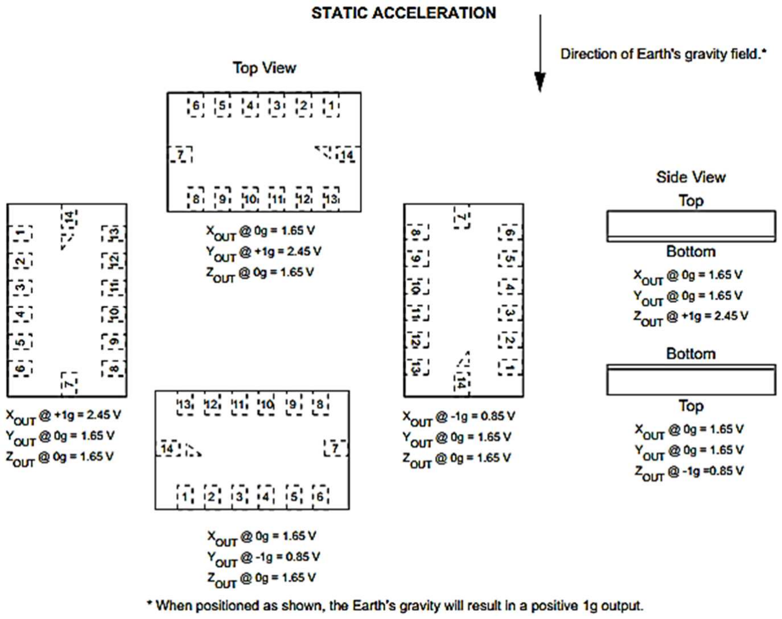
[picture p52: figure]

Figura 4: Aceleración Estática.

### DESCRIPCIÓN

Se trata de una tarjeta que incluye un sensor acelerómetro MMA7361L de tres ejes analógico de Freescale. Esta board cuenta con:

### 1. Entrada de voltaje de 5 V y 3.3 V

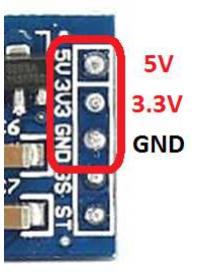
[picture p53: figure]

Figura 5: Pines entrada de voltaje.

6

El sensor de aceleración trabaja a 3.3V, lo que lo hace muy económico en consumo, pero la tarjeta cuenta con dos entradas de voltaje 5V, y 3.3V

Si la alimentas con 5V, se activa un regulador de 3.3V para energizar el sensor, de lo contrario si se utilizan 3.3V se alimentaria directamente el sensor, además cuenta con el pin GND para la tierra o negativo.

Advertencia: Se debe tener mucha precaución en no invertir la polaridad del voltaje de entrada, puesto que puede ocasionar daños en la tarjeta.

### 2. Regulador a 3.3V

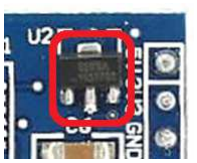
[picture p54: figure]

Figura 3: Regulador de 5V. Este regulador permite tomar el voltaje de entrada (entre 7V - 5V), y arrojar 3.3V a la parte del sensor pin 6 (Figura 2).

Advertencia: Se debe tener el voltaje que soporta el regulador para no dañarlo.

### 3. Pines analógicos de salida

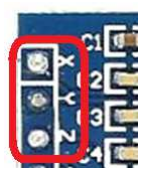
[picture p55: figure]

Figura 4: Pines Análogos de salida La tarjeta cuenta con tres pines analógicos que expresan as coordenadas X, Y, y Z, las cuales representan un voltaje en movimiento del sensor en el eje correspondiente.

Advertencia: Se debe tener en cuenta que son salidas y no entradas de voltaje

7

### 4. Pines de control

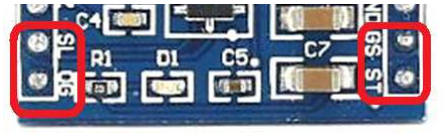
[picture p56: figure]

Figura 5: Pines de control.

La tarjeta cuenta con tres pines de control y uno de salida digital, es decir;

ST: Self Test

El sensor proporciona una función de auto verificación que permite la verificación de la integridad mecánica y eléctrica del acelerómetro en cualquier momento antes o después de la instalación. Esta característica es fundamental en aplicaciones tales como la protección de la unidad de disco duro en el que la integridad del sistema debe asegurar durante la vida útil del producto. Los clientes pueden utilizar de prueba automática para verificar la capacidad de soldadura para confirmar que la pieza se monta a la PCB correctamente. Para utilizar esta característica para verificar la función 0g-Detect, el acelerómetro se coloca boca abajo para que el eje z experimente -1g. Cuando se inicia la función de auto-test, una fuerza electrostática se aplica a cada eje para hacer que se desvíe. El eje X y Y se desvían ligeramente mientras que el eje Z se recorta para desviar 1g. Este procedimiento asegura que tanto la mecánica (g-cell) y partes electrónicas del acelerómetro están funcionando.

0G: 0g-Detect

El sensor ofrece una función que proporciona una señal lógica alta cuando los tres ejes están en 0g. Esta característica permite a la aplicación de la protección lineal caída libre si la señal está conectado a un pin de interrupción o un pin de E / S de monitoreo en un micro-controlador.

8

GS: g-Select

Esta característica permite la selección entre dos sensibilidades, esto de la entrada lógica colocado en el pin 10, la ganancia interna del dispositivo se cambia permitiendo que funcione con una o sensibilidad 1,5 g o 6 g (Tabla 1). Esta característica es ideal cuando un producto tiene aplicaciones que requieren dos sensibilidades diferentes para un rendimiento óptimo.

La sensibilidad se puede cambiar en cualquier momento durante la operación del producto, el pin se puede dejar desconectado para aplicaciones que requieren sólo una sensibilidad de 1,5 g.

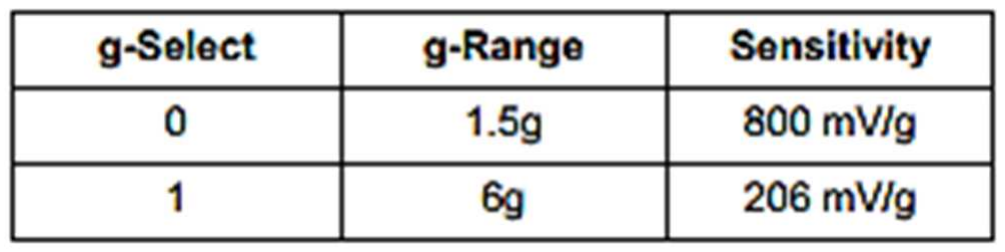
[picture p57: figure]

Tabla 1: Ajuste de Sensibilidad.

SL: Sleep Mode

El acelerómetro de 3 ejes proporciona un modo de reposo que es ideal para la batería. Cuando el modo de apagado está activado, las salidas del dispositivo están apagados, proporcionando una reducción significativa de la corriente de funcionamiento. Una señal de entrada de nivel bajo en el pin 7 (Modo de suspensión) coloca el dispositivo en este modo y reduce la corriente a 3 µA tip. Para el consumo de energía más bajo, se recomienda fijar g-Select el modo de 1,5 g. Mediante la colocación de señales altas de entrada en el pin 7, el dispositivo se reanudará al modo normal de operación.

Advertencia: Se debe tener en cuenta acoplar o unir las tierras con el montaje que se utiliza, esto para el buen funcionamiento de este dispositivo.

### 5. Indicador de encendido

Figura 6: Led de encendido.

9

La tarjeta cuenta con un Led de encendido, el cual prenderá a penas se alimente la tarjeta, como se especifica en el item 1.

Resumen

- Bajo Consumo de corriente: 400 µA
- Modo de espera: 3 µA
- Operación de baja tensión: 2,2 V - 3,6 V
- Alta sensibilidad (800 mV / g@1.5g)
- Sensibilidad seleccionable (± 1,5 g, ± 6 g)
- Vuelta rápida Tiempo de calentamiento (0.5 ms Tiempo de Respuesta Activa)
- Self Test para comprobar funcionamiento.
- 0 g-Detect para la Protección de la caída libre
- El condicionamiento de señal con filtro de paso bajo

Para mayor información consulte el DataSheet: http://1drv.ms/XCaVTz

### FUNCIONAMIENTO

Ahora trataremos de realizar un ejemplo básico de funcionamiento, el cual describiremos por paso, el objetivo es mostrar el funcionamiento de la tarjeta, con ayuda de un Arduino.

Paso uno: Instalar la librería del acelerómetro para Arduino.

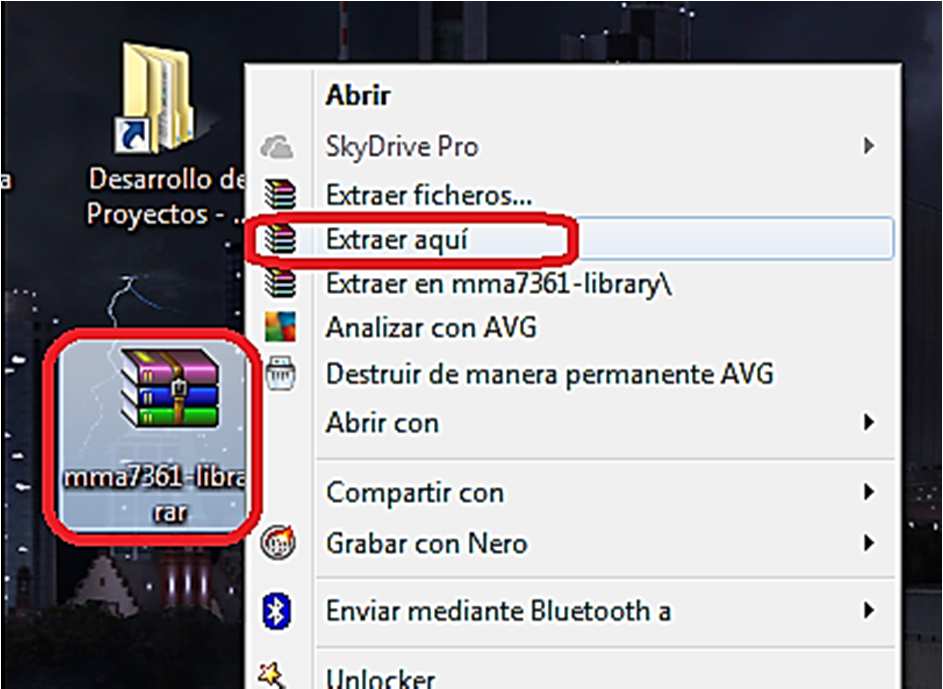
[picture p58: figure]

Figura 7: Ubicación de la librería.

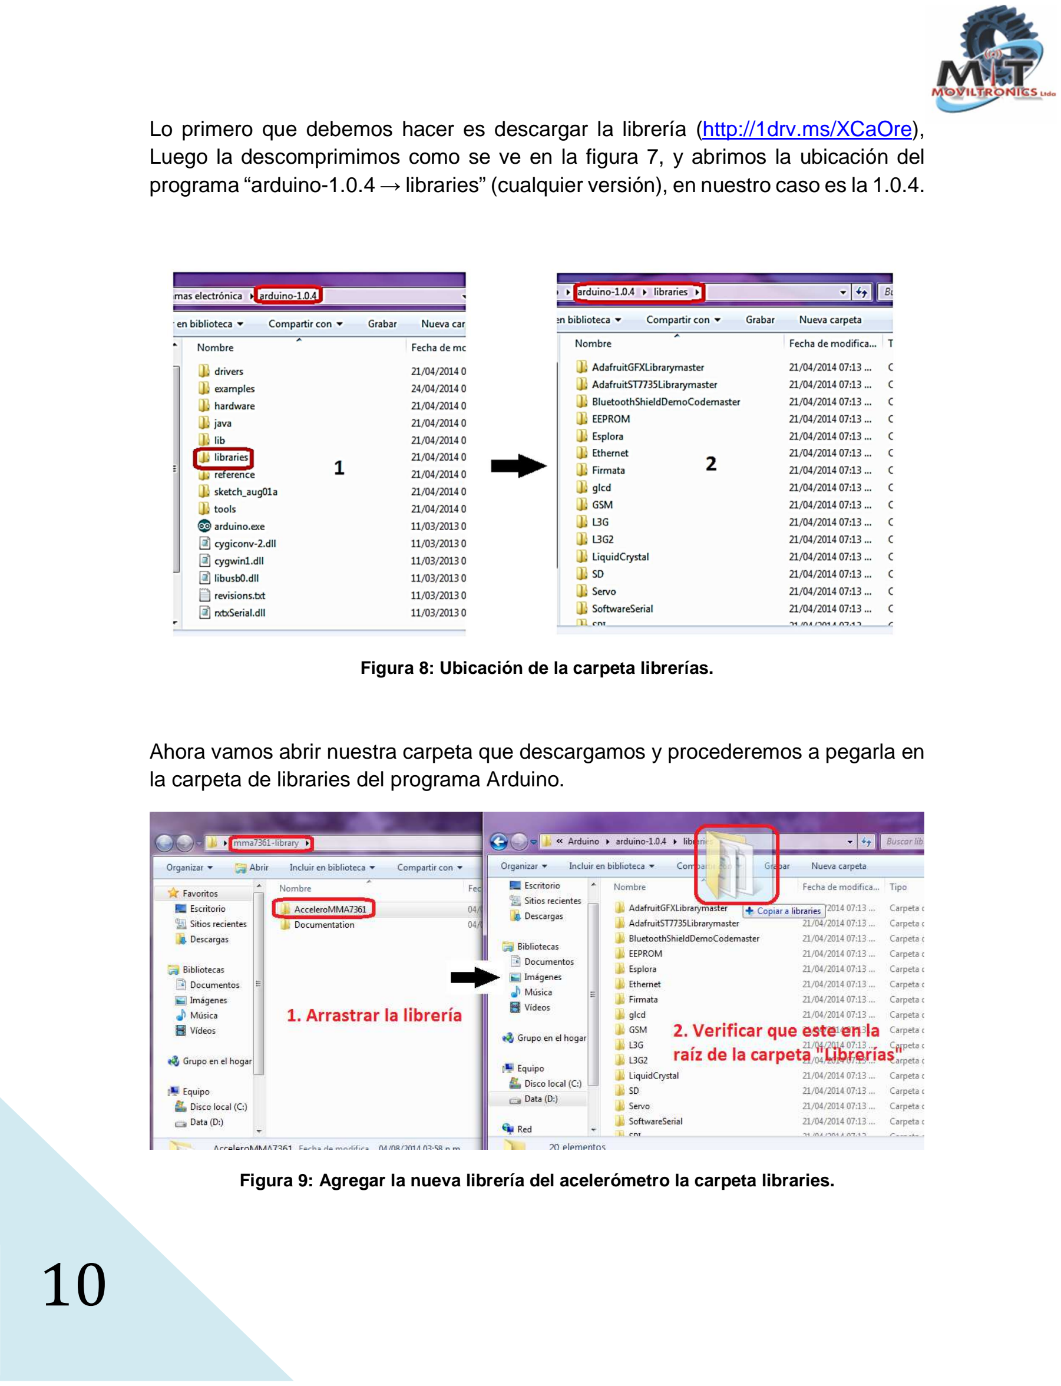
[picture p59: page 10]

10

Lo primero que debemos hacer es descargar la librería (http://1drv.ms/XCaOre), Luego la descomprimimos como se ve en la figura 7, y abrimos la ubicación del programa “arduino-1.0.4 → libraries” (cualquier versión), en nuestro caso es la 1.0.4.

Figura 8: Ubicación de la carpeta librerías.

Ahora vamos abrir nuestra carpeta que descargamos y procederemos a pegarla en la carpeta de libraries del programa Arduino.

Figura 9: Agregar la nueva librería del acelerómetro la carpeta libraries.

11

Paso dos: Ejecutar el Software Arduino.

Figura 9: Arduino 1.0.4

Vamos a abrir el software “arduino.exe”, luego vamos a la ruta que muestra en la figura 10.

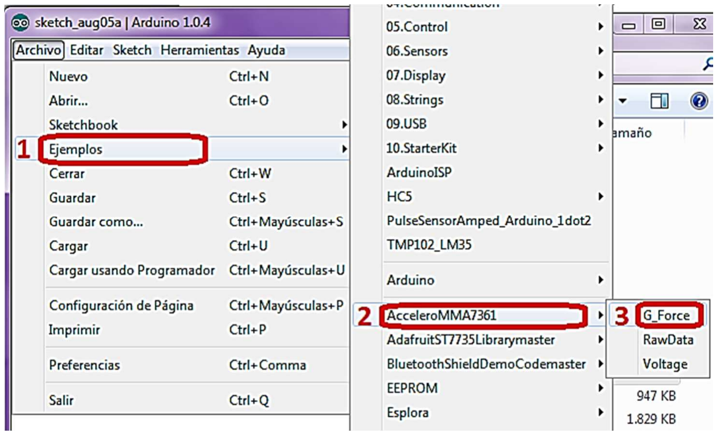
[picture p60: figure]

Figura 10: Ruta ejemplo “G_Force” del acelerómetro.

Allí se mostrara un código ejemplo, figura 11.

12

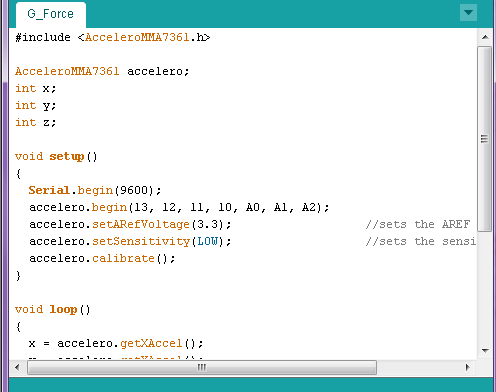
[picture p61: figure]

Figura 11: Ejemplo “G_Force” del acelerómetro.

Paso tres: Pines a utilizar.

Arduino Uno MMA7361 - Acelerómetro 13 SL (Sleep)
12 ST (SelfTest)
11 0G (zeroG)
10 GS (gSelect)
A0 | X
A1 | Y
A2 | Z
3.3V | 3.3V
GND | GND

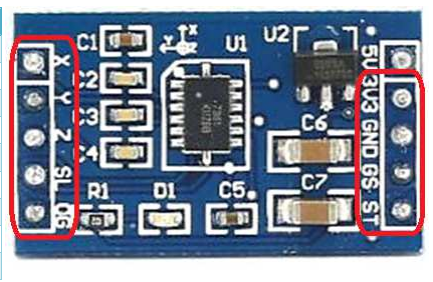
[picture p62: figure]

Figura 12: Pines a utilizar.

Tenemos que identificar que pines vamos a utilizar para la tarjeta, debemos tener en cuenta que se debe realizar un puente entre dos pines del Arduino AREF con 3.3V, esto permite que realice una lectura analógica de los datos de acelerómetro más precisa.

Hay que recordar que la sensibilidad está en bajo, (Ver tabla 1).

13

Paso cuatro: Montaje final.

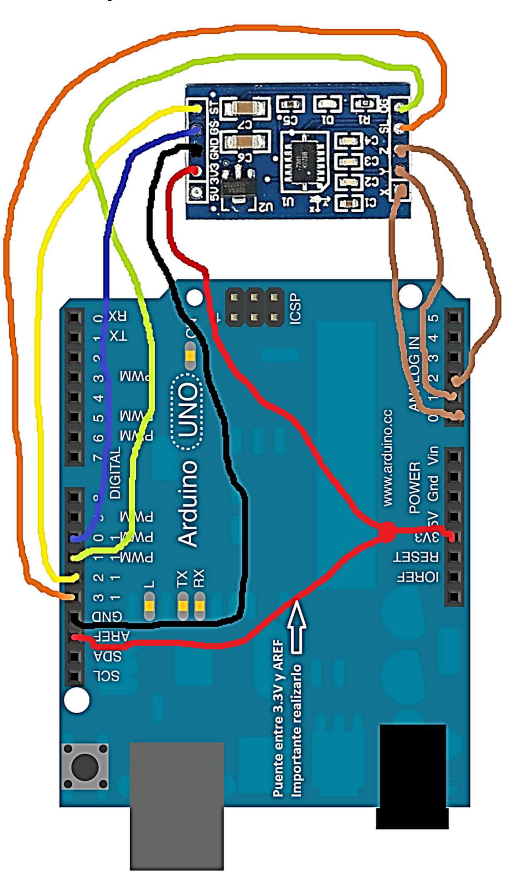
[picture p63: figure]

Figura 11: Montaje de ejemplo.

14

En la figura 11 se presenta el montaje que se va a utilizar para leer los datos del acelerómetro, después de haber programado el Arduino, vamos a abrir el terminal,
y verificar la velocidad de 9600 (Después de haber programado el Arduino).


Figura 12: Datos de salida.

Ahora podrás tomar el acelerómetro, e inclinarlo, y ver la variación.

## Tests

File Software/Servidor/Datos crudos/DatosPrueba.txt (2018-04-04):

 
 db.temperaturas.insert({valor: -10, fecha:"2018/3/31", hora: "00:00:00", fechaSys: ISODate("2018-03-31-T00:00:00.0Z")})
 
 db.temperaturas.insert({valor: -5, fecha:"2018/3/31", hora: "01:00:00", fechaSys: ISODate("2018-03-31-T01:00:00.0Z")})
 
 db.temperaturas.insert({valor: -3, fecha:"2018/3/31", hora: "02:00:00", fechaSys: ISODate("2018-03-31-T02:00:00.0Z")})
 
 db.temperaturas.insert({valor: 0, fecha:"2018/3/31", hora: "03:00:00", fechaSys: ISODate("2018-03-31-T03:00:00.0Z")})
 
 db.temperaturas.insert({valor: 3, fecha:"2018/3/31", hora: "04:00:00", fechaSys: ISODate("2018-03-31-T04:00:00.0Z")})
 
 db.temperaturas.insert({valor: 5, fecha:"2018/3/31", hora: "05:00:00", fechaSys: ISODate("2018-03-31-T05:00:00.0Z")})
 
 db.temperaturas.insert({valor: 8, fecha:"2018/3/31", hora: "06:00:00", fechaSys: ISODate("2018-03-31-T06:00:00.0Z")})
 
 db.temperaturas.insert({valor: 11, fecha:"2018/3/31", hora: "07:00:00", fechaSys: ISODate("2018-03-31-T07:00:00.0Z")})
 
 db.temperaturas.insert({valor: 13, fecha:"2018/3/31", hora: "08:00:00", fechaSys: ISODate("2018-03-31-T08:00:00.0Z")})
 
 db.temperaturas.insert({valor: 16, fecha:"2018/3/31", hora: "09:00:00", fechaSys: ISODate("2018-03-31-T09:00:00.0Z")})
 
 db.temperaturas.insert({valor: 17, fecha:"2018/3/31", hora: "10:00:00", fechaSys: ISODate("2018-03-31-T10:00:00.0Z")})
 
 db.temperaturas.insert({valor: 18, fecha:"2018/3/31", hora: "11:00:00", fechaSys: ISODate("2018-03-31-T11:00:00.0Z")})
 
 db.temperaturas.insert({valor: 20, fecha:"2018/3/31", hora: "12:00:00", fechaSys: ISODate("2018-03-31-T12:00:00.0Z")})
 
 db.temperaturas.insert({valor: 22, fecha:"2018/3/31", hora: "13:00:00", fechaSys: ISODate("2018-03-31-T13:00:00.0Z")})
 
 db.temperaturas.insert({valor: 25, fecha:"2018/3/31", hora: "14:00:00", fechaSys: ISODate("2018-03-31-T14:00:00.0Z")})
 
 db.temperaturas.insert({valor: 30, fecha:"2018/3/31", hora: "15:00:00", fechaSys: ISODate("2018-03-31-T15:00:00.0Z")})
 
 db.temperaturas.insert({valor: 30, fecha:"2018/3/31", hora: "16:00:00", fechaSys: ISODate("2018-03-31-T16:00:00.0Z")})
 
 db.temperaturas.insert({valor: 25, fecha:"2018/3/31", hora: "17:00:00", fechaSys: ISODate("2018-03-31-T17:00:00.0Z")})
 
 db.temperaturas.insert({valor: 20, fecha:"2018/3/31", hora: "18:00:00", fechaSys: ISODate("2018-03-31-T18:00:00.0Z")})
 
 db.temperaturas.insert({valor: 18, fecha:"2018/3/31", hora: "19:00:00", fechaSys: ISODate("2018-03-31-T19:00:00.0Z")})
  
 db.temperaturas.insert({valor: 15, fecha:"2018/3/31", hora: "20:00:00", fechaSys: ISODate("2018-03-31-T20:00:00.0Z")})
   
 db.temperaturas.insert({valor: 11, fecha:"2018/3/31", hora: "21:00:00", fechaSys: ISODate("2018-03-31-T21:00:00.0Z")})
	
 db.temperaturas.insert({valor: 8, fecha:"2018/3/31", hora: "22:00:00", fechaSys: ISODate("2018-03-31-T22:00:00.0Z")})
	 
 db.temperaturas.insert({valor: 2, fecha:"2018/3/31", hora: "23:00:00", fechaSys: ISODate("2018-03-31-T23:00:00.0Z")})

 db.temperaturas.insert({valor: 3, fecha:"2018/3/31", hora: "18:00:00", fechaSys: ISODate("2018-03-31-T10:00:00.0Z")})

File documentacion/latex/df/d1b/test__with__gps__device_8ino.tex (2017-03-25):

\hypertarget{test__with__gps__device_8ino}{}\section{Referencia del Archivo Test/\+G\+P\+S/\+Tiny\+G\+P\+S/\+Tiny\+G\+P\+S/examples/test\+\_\+with\+\_\+gps\+\_\+device/test\+\_\+with\+\_\+gps\+\_\+device.ino}
\label{test__with__gps__device_8ino}\index{Test/\+G\+P\+S/\+Tiny\+G\+P\+S/\+Tiny\+G\+P\+S/examples/test\+\_\+with\+\_\+gps\+\_\+device/test\+\_\+with\+\_\+gps\+\_\+device.\+ino@{Test/\+G\+P\+S/\+Tiny\+G\+P\+S/\+Tiny\+G\+P\+S/examples/test\+\_\+with\+\_\+gps\+\_\+device/test\+\_\+with\+\_\+gps\+\_\+device.\+ino}}
{\ttfamily \#include $<$Software\+Serial.\+h$>$}\newline
{\ttfamily \#include $<$Tiny\+G\+P\+S.\+h$>$}\newline
\subsection*{Funciones}
\begin{DoxyCompactItemize}
\item 
Software\+Serial \hyperlink{test__with__gps__device_8ino_ad6146be3f2c4ff5ac64c90ef5d1b37b1}{ss} (4, 3)
\item 
void \hyperlink{test__with__gps__device_8ino_a4fc01d736fe50cf5b977f755b675f11d}{setup} ()
\item 
void \hyperlink{test__with__gps__device_8ino_afe461d27b9c48d5921c00d521181f12f}{loop} ()
\end{DoxyCompactItemize}
\subsection*{Variables}
\begin{DoxyCompactItemize}
\item 
\hyperlink{class_tiny_g_p_s}{Tiny\+G\+PS} \hyperlink{test__with__gps__device_8ino_a4e2f9a5d1b23f30f530101af71f72744}{gps}
\end{DoxyCompactItemize}

\subsection{Documentación de las funciones}
\mbox{\Hypertarget{test__with__gps__device_8ino_afe461d27b9c48d5921c00d521181f12f}\label{test__with__gps__device_8ino_afe461d27b9c48d5921c00d521181f12f}} 
\index{test\+\_\+with\+\_\+gps\+\_\+device.\+ino@{test\+\_\+with\+\_\+gps\+\_\+device.\+ino}!loop@{loop}}
\index{loop@{loop}!test\+\_\+with\+\_\+gps\+\_\+device.\+ino@{test\+\_\+with\+\_\+gps\+\_\+device.\+ino}}
\subsubsection{\texorpdfstring{loop()}{loop()}}
{\footnotesize\ttfamily void loop (\begin{DoxyParamCaption}{ }\end{DoxyParamCaption})}

Definición en la línea 33 del archivo test\+\_\+with\+\_\+gps\+\_\+device.\+ino.

\mbox{\Hypertarget{test__with__gps__device_8ino_a4fc01d736fe50cf5b977f755b675f11d}\label{test__with__gps__device_8ino_a4fc01d736fe50cf5b977f755b675f11d}} 
\index{test\+\_\+with\+\_\+gps\+\_\+device.\+ino@{test\+\_\+with\+\_\+gps\+\_\+device.\+ino}!setup@{setup}}
\index{setup@{setup}!test\+\_\+with\+\_\+gps\+\_\+device.\+ino@{test\+\_\+with\+\_\+gps\+\_\+device.\+ino}}
\subsubsection{\texorpdfstring{setup()}{setup()}}
{\footnotesize\ttfamily void setup (\begin{DoxyParamCaption}{ }\end{DoxyParamCaption})}

Definición en la línea 19 del archivo test\+\_\+with\+\_\+gps\+\_\+device.\+ino.

\mbox{\Hypertarget{test__with__gps__device_8ino_ad6146be3f2c4ff5ac64c90ef5d1b37b1}\label{test__with__gps__device_8ino_ad6146be3f2c4ff5ac64c90ef5d1b37b1}} 
\index{test\+\_\+with\+\_\+gps\+\_\+device.\+ino@{test\+\_\+with\+\_\+gps\+\_\+device.\+ino}!ss@{ss}}
\index{ss@{ss}!test\+\_\+with\+\_\+gps\+\_\+device.\+ino@{test\+\_\+with\+\_\+gps\+\_\+device.\+ino}}
\subsubsection{\texorpdfstring{ss()}{ss()}}
{\footnotesize\ttfamily Software\+Serial ss (\begin{DoxyParamCaption}\item[{4}]{,  }\item[{3}]{ }\end{DoxyParamCaption})}

\subsection{Documentación de las variables}
\mbox{\Hypertarget{test__with__gps__device_8ino_a4e2f9a5d1b23f30f530101af71f72744}\label{test__with__gps__device_8ino_a4e2f9a5d1b23f30f530101af71f72744}} 
\index{test\+\_\+with\+\_\+gps\+\_\+device.\+ino@{test\+\_\+with\+\_\+gps\+\_\+device.\+ino}!gps@{gps}}
\index{gps@{gps}!test\+\_\+with\+\_\+gps\+\_\+device.\+ino@{test\+\_\+with\+\_\+gps\+\_\+device.\+ino}}
\subsubsection{\texorpdfstring{gps}{gps}}
{\footnotesize\ttfamily \hyperlink{class_tiny_g_p_s}{Tiny\+G\+PS} gps}

Definición en la línea 10 del archivo test\+\_\+with\+\_\+gps\+\_\+device.\+ino.

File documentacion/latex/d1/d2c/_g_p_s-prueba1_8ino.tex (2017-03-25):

\hypertarget{_g_p_s-prueba1_8ino}{}\section{Referencia del Archivo Test/\+G\+P\+S/\+G\+P\+S-\/prueba1/\+G\+P\+S-\/prueba1.ino}
\label{_g_p_s-prueba1_8ino}\index{Test/\+G\+P\+S/\+G\+P\+S-\/prueba1/\+G\+P\+S-\/prueba1.\+ino@{Test/\+G\+P\+S/\+G\+P\+S-\/prueba1/\+G\+P\+S-\/prueba1.\+ino}}
{\ttfamily \#include $<$Software\+Serial.\+h$>$}\newline
\subsection*{Funciones}
\begin{DoxyCompactItemize}
\item 
Software\+Serial \hyperlink{_g_p_s-prueba1_8ino_a2dcf99faa4fe24fd03cda4a01ac4ce1c}{gps} (4, 3)
\item 
void \hyperlink{_g_p_s-prueba1_8ino_a4fc01d736fe50cf5b977f755b675f11d}{setup} ()
\item 
void \hyperlink{_g_p_s-prueba1_8ino_afe461d27b9c48d5921c00d521181f12f}{loop} ()
\end{DoxyCompactItemize}
\subsection*{Variables}
\begin{DoxyCompactItemize}
\item 
char \hyperlink{_g_p_s-prueba1_8ino_a27c4b81ab2ec9e3399303a0e0398c36d}{dato} =\textquotesingle{} \textquotesingle{}
\end{DoxyCompactItemize}

\subsection{Documentación de las funciones}
\mbox{\Hypertarget{_g_p_s-prueba1_8ino_a2dcf99faa4fe24fd03cda4a01ac4ce1c}\label{_g_p_s-prueba1_8ino_a2dcf99faa4fe24fd03cda4a01ac4ce1c}} 
\index{G\+P\+S-\/prueba1.\+ino@{G\+P\+S-\/prueba1.\+ino}!gps@{gps}}
\index{gps@{gps}!G\+P\+S-\/prueba1.\+ino@{G\+P\+S-\/prueba1.\+ino}}
\subsubsection{\texorpdfstring{gps()}{gps()}}
{\footnotesize\ttfamily Software\+Serial gps (\begin{DoxyParamCaption}\item[{4}]{,  }\item[{3}]{ }\end{DoxyParamCaption})}

Esta prueba, se basa en obtener una trama para luego formatearla. Para ello se hace uso de la librería \hyperlink{class_tiny_g_p_s}{Tiny\+G\+PS}, para acceder a la trama de datos. La prueba no resultó satisfactorio en cuanto a la conexión La señal gps, se obtiene pero con errores. Hay que efectuar una nueva prueba desde un ambiente despejado.

simple\+\_\+test que ofrece la librería funciona marcando algunos errores de trama. \mbox{[}gps description\mbox{]} 
\begin{DoxyParams}{Parámetros}
{\em \mbox{[}rx\mbox{]}} & \mbox{[}pin recepción\mbox{]} \\
\hline
{\em \mbox{[}tx\mbox{]}} & \mbox{[}pin transmisión\mbox{]} \\
\hline
\end{DoxyParams}
\begin{DoxyReturn}{Devuelve}
\mbox{[}Software\+Serial\mbox{]} 
\end{DoxyReturn}
\mbox{\Hypertarget{_g_p_s-prueba1_8ino_afe461d27b9c48d5921c00d521181f12f}\label{_g_p_s-prueba1_8ino_afe461d27b9c48d5921c00d521181f12f}} 
\index{G\+P\+S-\/prueba1.\+ino@{G\+P\+S-\/prueba1.\+ino}!loop@{loop}}
\index{loop@{loop}!G\+P\+S-\/prueba1.\+ino@{G\+P\+S-\/prueba1.\+ino}}
\subsubsection{\texorpdfstring{loop()}{loop()}}
{\footnotesize\ttfamily void loop (\begin{DoxyParamCaption}{ }\end{DoxyParamCaption})}

Definición en la línea 27 del archivo G\+P\+S-\/prueba1.\+ino.

\mbox{\Hypertarget{_g_p_s-prueba1_8ino_a4fc01d736fe50cf5b977f755b675f11d}\label{_g_p_s-prueba1_8ino_a4fc01d736fe50cf5b977f755b675f11d}} 
\index{G\+P\+S-\/prueba1.\+ino@{G\+P\+S-\/prueba1.\+ino}!setup@{setup}}
\index{setup@{setup}!G\+P\+S-\/prueba1.\+ino@{G\+P\+S-\/prueba1.\+ino}}
\subsubsection{\texorpdfstring{setup()}{setup()}}
{\footnotesize\ttfamily void setup (\begin{DoxyParamCaption}{ }\end{DoxyParamCaption})}

Definición en la línea 20 del archivo G\+P\+S-\/prueba1.\+ino.

\subsection{Documentación de las variables}
\mbox{\Hypertarget{_g_p_s-prueba1_8ino_a27c4b81ab2ec9e3399303a0e0398c36d}\label{_g_p_s-prueba1_8ino_a27c4b81ab2ec9e3399303a0e0398c36d}} 
\index{G\+P\+S-\/prueba1.\+ino@{G\+P\+S-\/prueba1.\+ino}!dato@{dato}}
\index{dato@{dato}!G\+P\+S-\/prueba1.\+ino@{G\+P\+S-\/prueba1.\+ino}}
\subsubsection{\texorpdfstring{dato}{dato}}
{\footnotesize\ttfamily char dato =\textquotesingle{} \textquotesingle{}}

Definición en la línea 18 del archivo G\+P\+S-\/prueba1.\+ino.

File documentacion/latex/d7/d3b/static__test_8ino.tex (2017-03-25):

\hypertarget{static__test_8ino}{}\section{Referencia del Archivo Test/\+G\+P\+S/\+Tiny\+G\+P\+S/\+Tiny\+G\+P\+S/examples/static\+\_\+test/static\+\_\+test.ino}
\label{static__test_8ino}\index{Test/\+G\+P\+S/\+Tiny\+G\+P\+S/\+Tiny\+G\+P\+S/examples/static\+\_\+test/static\+\_\+test.\+ino@{Test/\+G\+P\+S/\+Tiny\+G\+P\+S/\+Tiny\+G\+P\+S/examples/static\+\_\+test/static\+\_\+test.\+ino}}
{\ttfamily \#include $<$Tiny\+G\+P\+S.\+h$>$}\newline
{\ttfamily \#include $<$avr\textbackslash{}pgmspace.\+h$>$}\newline
\subsection*{Funciones}
\begin{DoxyCompactItemize}
\item 
void \hyperlink{static__test_8ino_a4fc01d736fe50cf5b977f755b675f11d}{setup} ()
\item 
void \hyperlink{static__test_8ino_afe461d27b9c48d5921c00d521181f12f}{loop} ()
\end{DoxyCompactItemize}
\subsection*{Variables}
\begin{DoxyCompactItemize}
\item 
prog\+\_\+char str1 \mbox{[}$\,$\mbox{]} \hyperlink{static__test_8ino_a37dd2e5939ed07e6228272db05427f31}{P\+R\+O\+G\+M\+EM} = \char`\"{}\$G\+P\+R\+MC,201547.\+000,A,3014.\+5527,N,09749.\+5808,W,0.\+24,163.\+05,040109,,$\ast$1\+A\char`\"{}
\item 
prog\+\_\+char $\ast$ \hyperlink{static__test_8ino_a0a3cd97c1566952d62849717668e2174}{teststrs} \mbox{[}4\mbox{]} = \{str1, str2, str3, str4\}
\end{DoxyCompactItemize}

\subsection{Documentación de las funciones}
\mbox{\Hypertarget{static__test_8ino_afe461d27b9c48d5921c00d521181f12f}\label{static__test_8ino_afe461d27b9c48d5921c00d521181f12f}} 
\index{static\+\_\+test.\+ino@{static\+\_\+test.\+ino}!loop@{loop}}
\index{loop@{loop}!static\+\_\+test.\+ino@{static\+\_\+test.\+ino}}
\subsubsection{\texorpdfstring{loop()}{loop()}}
{\footnotesize\ttfamily void loop (\begin{DoxyParamCaption}{ }\end{DoxyParamCaption})}

Definición en la línea 43 del archivo static\+\_\+test.\+ino.

\mbox{\Hypertarget{static__test_8ino_a4fc01d736fe50cf5b977f755b675f11d}\label{static__test_8ino_a4fc01d736fe50cf5b977f755b675f11d}} 
\index{static\+\_\+test.\+ino@{static\+\_\+test.\+ino}!setup@{setup}}
\index{setup@{setup}!static\+\_\+test.\+ino@{static\+\_\+test.\+ino}}
\subsubsection{\texorpdfstring{setup()}{setup()}}
{\footnotesize\ttfamily void setup (\begin{DoxyParamCaption}{ }\end{DoxyParamCaption})}

Definición en la línea 21 del archivo static\+\_\+test.\+ino.

\subsection{Documentación de las variables}
\mbox{\Hypertarget{static__test_8ino_a37dd2e5939ed07e6228272db05427f31}\label{static__test_8ino_a37dd2e5939ed07e6228272db05427f31}} 
\index{static\+\_\+test.\+ino@{static\+\_\+test.\+ino}!P\+R\+O\+G\+M\+EM@{P\+R\+O\+G\+M\+EM}}
\index{P\+R\+O\+G\+M\+EM@{P\+R\+O\+G\+M\+EM}!static\+\_\+test.\+ino@{static\+\_\+test.\+ino}}
\subsubsection{\texorpdfstring{P\+R\+O\+G\+M\+EM}{PROGMEM}}
{\footnotesize\ttfamily prog\+\_\+char str4 \mbox{[}$\,$\mbox{]} P\+R\+O\+G\+M\+EM = \char`\"{}\$G\+P\+R\+MC,201547.\+000,A,3014.\+5527,N,09749.\+5808,W,0.\+24,163.\+05,040109,,$\ast$1\+A\char`\"{}}

Definición en la línea 8 del archivo static\+\_\+test.\+ino.

\mbox{\Hypertarget{static__test_8ino_a0a3cd97c1566952d62849717668e2174}\label{static__test_8ino_a0a3cd97c1566952d62849717668e2174}} 
\index{static\+\_\+test.\+ino@{static\+\_\+test.\+ino}!teststrs@{teststrs}}
\index{teststrs@{teststrs}!static\+\_\+test.\+ino@{static\+\_\+test.\+ino}}
\subsubsection{\texorpdfstring{teststrs}{teststrs}}
{\footnotesize\ttfamily prog\+\_\+char$\ast$ teststrs\mbox{[}4\mbox{]} = \{str1, str2, str3, str4\}}

Definición en la línea 12 del archivo static\+\_\+test.\+ino.

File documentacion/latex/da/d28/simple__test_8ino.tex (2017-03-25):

\hypertarget{simple__test_8ino}{}\section{Referencia del Archivo Test/\+G\+P\+S/\+Tiny\+G\+P\+S/\+Tiny\+G\+P\+S/examples/simple\+\_\+test/simple\+\_\+test.ino}
\label{simple__test_8ino}\index{Test/\+G\+P\+S/\+Tiny\+G\+P\+S/\+Tiny\+G\+P\+S/examples/simple\+\_\+test/simple\+\_\+test.\+ino@{Test/\+G\+P\+S/\+Tiny\+G\+P\+S/\+Tiny\+G\+P\+S/examples/simple\+\_\+test/simple\+\_\+test.\+ino}}
{\ttfamily \#include $<$Software\+Serial.\+h$>$}\newline
{\ttfamily \#include $<$Tiny\+G\+P\+S.\+h$>$}\newline
\subsection*{Funciones}
\begin{DoxyCompactItemize}
\item 
Software\+Serial \hyperlink{simple__test_8ino_ad6146be3f2c4ff5ac64c90ef5d1b37b1}{ss} (4, 3)
\item 
void \hyperlink{simple__test_8ino_a4fc01d736fe50cf5b977f755b675f11d}{setup} ()
\item 
void \hyperlink{simple__test_8ino_afe461d27b9c48d5921c00d521181f12f}{loop} ()
\end{DoxyCompactItemize}
\subsection*{Variables}
\begin{DoxyCompactItemize}
\item 
\hyperlink{class_tiny_g_p_s}{Tiny\+G\+PS} \hyperlink{simple__test_8ino_a4e2f9a5d1b23f30f530101af71f72744}{gps}
\end{DoxyCompactItemize}

\subsection{Documentación de las funciones}
\mbox{\Hypertarget{simple__test_8ino_afe461d27b9c48d5921c00d521181f12f}\label{simple__test_8ino_afe461d27b9c48d5921c00d521181f12f}} 
\index{simple\+\_\+test.\+ino@{simple\+\_\+test.\+ino}!loop@{loop}}
\index{loop@{loop}!simple\+\_\+test.\+ino@{simple\+\_\+test.\+ino}}
\subsubsection{\texorpdfstring{loop()}{loop()}}
{\footnotesize\ttfamily void loop (\begin{DoxyParamCaption}{ }\end{DoxyParamCaption})}

Definición en la línea 23 del archivo simple\+\_\+test.\+ino.

\mbox{\Hypertarget{simple__test_8ino_a4fc01d736fe50cf5b977f755b675f11d}\label{simple__test_8ino_a4fc01d736fe50cf5b977f755b675f11d}} 
\index{simple\+\_\+test.\+ino@{simple\+\_\+test.\+ino}!setup@{setup}}
\index{setup@{setup}!simple\+\_\+test.\+ino@{simple\+\_\+test.\+ino}}
\subsubsection{\texorpdfstring{setup()}{setup()}}
{\footnotesize\ttfamily void setup (\begin{DoxyParamCaption}{ }\end{DoxyParamCaption})}

Definición en la línea 13 del archivo simple\+\_\+test.\+ino.

\mbox{\Hypertarget{simple__test_8ino_ad6146be3f2c4ff5ac64c90ef5d1b37b1}\label{simple__test_8ino_ad6146be3f2c4ff5ac64c90ef5d1b37b1}} 
\index{simple\+\_\+test.\+ino@{simple\+\_\+test.\+ino}!ss@{ss}}
\index{ss@{ss}!simple\+\_\+test.\+ino@{simple\+\_\+test.\+ino}}
\subsubsection{\texorpdfstring{ss()}{ss()}}
{\footnotesize\ttfamily Software\+Serial ss (\begin{DoxyParamCaption}\item[{4}]{,  }\item[{3}]{ }\end{DoxyParamCaption})}

\subsection{Documentación de las variables}
\mbox{\Hypertarget{simple__test_8ino_a4e2f9a5d1b23f30f530101af71f72744}\label{simple__test_8ino_a4e2f9a5d1b23f30f530101af71f72744}} 
\index{simple\+\_\+test.\+ino@{simple\+\_\+test.\+ino}!gps@{gps}}
\index{gps@{gps}!simple\+\_\+test.\+ino@{simple\+\_\+test.\+ino}}
\subsubsection{\texorpdfstring{gps}{gps}}
{\footnotesize\ttfamily \hyperlink{class_tiny_g_p_s}{Tiny\+G\+PS} gps}

Definición en la línea 10 del archivo simple\+\_\+test.\+ino.

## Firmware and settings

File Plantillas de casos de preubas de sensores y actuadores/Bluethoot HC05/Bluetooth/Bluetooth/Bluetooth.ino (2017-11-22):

#include <SoftwareSerial.h>

SoftwareSerial bluetooth(10, 11); // RX, TX

void setup()
{
// Open serial communications and wait for port to open:
Serial.begin(9600);
bluetooth.begin(9600);
}

void loop() // run over and over
{
if ( bluetooth.available())
Serial.write( bluetooth.read());
if (Serial.available())
bluetooth.write(Serial.read());
}

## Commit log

2017-03-25 Creacion de proyecto en ATOM con platformio
2017-03-25 Agregando directorio de documentacion
2017-03-25 Archivo generador para documentación
2017-03-25 Realizando documentación de GPS y Bluetooth
2017-03-28 Documentacion de humedad y temperatura
2017-03-29 Pruebas de WIfi, por un lado la carpeta comandosAT, que nos sirve para configurar el módulo wifi esp8266 Además tenemos la prueba de velocidad, que no se ha finalizado su edición.
2017-03-29 Pruebas sobre el modulo wifi
2017-03-30 Codigos de pruebas, cam y temp
2017-04-06 Agregando documentación de modulo
2017-04-25 Agregado pruebas ultrasonido y servomotores
2017-04-26 Se agrega el modulo microSD
2017-04-26 Testeo de sensores
2017-04-26 Agregado pruebas de comuncacion a traves de serie
2017-05-12 Agregando serie dos arduinos
2017-09-20 Aplicacion raspberry nuevo directorio donde se almacena la aplicacion del sa
2017-10-24 Prueba sensores
2017-11-03 Botones con eventos de entrada y salida
2017-11-03 Agregado sensor ultrasonido
2017-11-03 Angular con recepcion de mensajes
2017-11-18 Nuevos directorios
    [Estimaciones de tiempo de desarrollo.xlsx, Rueda.skp, Tesis-base sola.stl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]
2017-11-21 Modificaciones en el Informe
2017-11-21 Primer punto de control de informe
2017-11-21 Agregado PDF primer punto de control
2017-11-22 Hay un bug en el servidor
2017-11-22 Agregando colecciones y devoluciones de json, agregando api con rutas para obtener temperatura gps etc
2017-12-05 Agregando esquemas de Fritzing
    [Sensor de GAS MQ-7.fzz, Sensor de temperatura DS18B20.fzz, Ultrasonidos.fzz]
2017-12-06 Tabla sensores finalizada
2018-01-19 Corrección de Informe Enero 2018
2018-02-01 Actualizacion
    Actualizacion de version de angular
2018-02-02 Agregado estadistica
    Agregando estadistica de temperaruta
2018-02-07 Agregado estadisticas
    Se agregaron las estadisticas, y las opciones para apagar y reiniciar.
    Falta definir en routes.js las rutas apagar y reinciar.
    Agregar script de apagado y reinicio.
    Verificar la bd en posteriores ejecuciones.
2018-02-09 Revision de correcciones
2018-02-17 Cambios capitulo 3
    Se corrige el capitulo3, se agregan la introducción y resumen de cap. Se corrigen los cambios solicitados en /root/tareas
2018-02-17 Finalización de CAPITULO 6
2018-02-22 Agregando scripts
    Agregando scripts y separacion de servidor y cliente
2018-03-01 Agregando estadisticas
    Correr la aplicacion angular forma publica
    Se agrega estadisticas de temperatura y monoxido
2018-03-05 Cambios en el informe
2018-03-08 Subiendo Archivos de configuración
2018-03-09 Agregado de Anexos
2018-03-15 Borrador de informe hasta capitulo 7
2018-03-17 Aplicacion cliente finalizada
    El cliente angular se encuentra finalizada con las estadáisticas y toma de datos
2018-03-24 Cambios en el software
    Cambios
2018-03-27 Cambios en el servidor
2018-04-03 revisiones cap10 y cap11
    [cuartoPisoFinal.skp, cuartoPisoFinal.stl]
2018-04-04 Uniendo anexo de codigos
2018-04-04 Borrador final - cap10
    [cuartoPisoFinal.skp, cuartoPisoFinalV2.stl]
2018-04-04 Raspberry commit
2018-04-06 Revision de borrador final hasta cap8
2018-04-07 Agregando informe de tesina hasta el capitulo 8
